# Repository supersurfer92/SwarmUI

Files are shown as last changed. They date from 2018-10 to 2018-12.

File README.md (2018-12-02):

# BadukBot: Swarming robots to play the game Go/Baduk

Based on Zooids: Building Blocks for Swarm User Interfaces

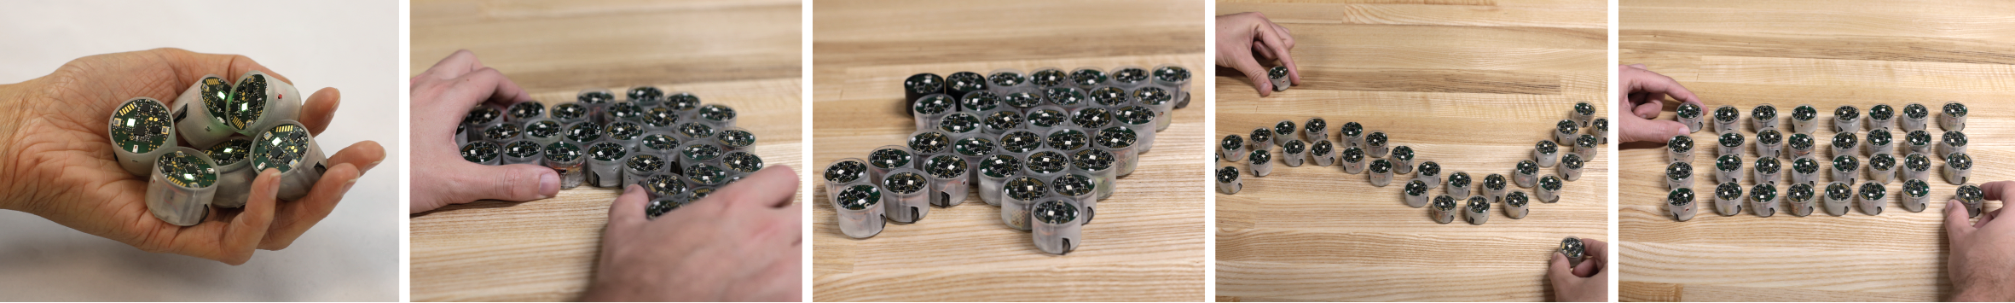
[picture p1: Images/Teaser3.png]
Teaser

Zooids, an open-source open-hardware platform for developing tabletop swarm interfaces, consist of a collection of custom-designed wheeled micro robots (each 2.6 cm in diameter), a radio base-station, a highspeed DLP structured light projector for optical tracking, and a software framework for application development and control.

Initial sketch of the redesigned Zooid, the BadukBot:
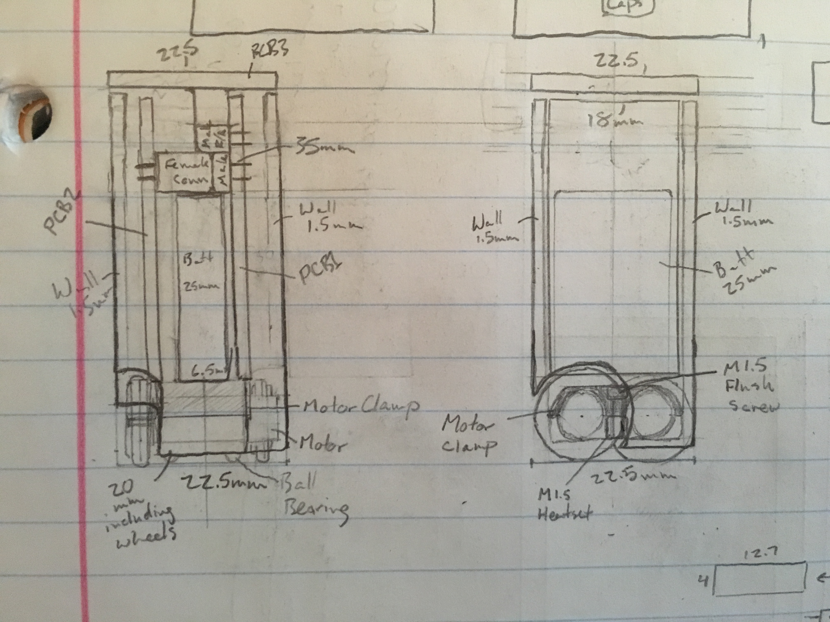
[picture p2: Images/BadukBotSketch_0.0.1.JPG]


Revision 3 of the new pcb:
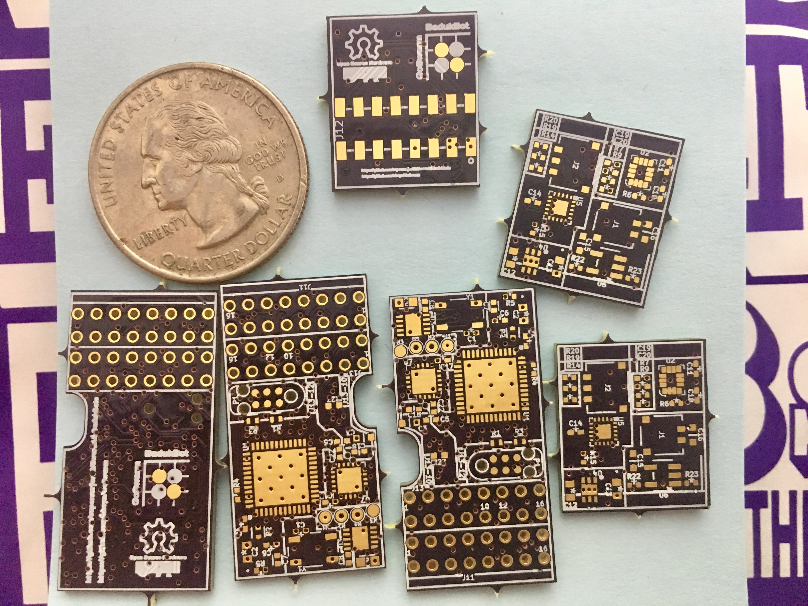
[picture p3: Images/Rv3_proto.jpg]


Original board:

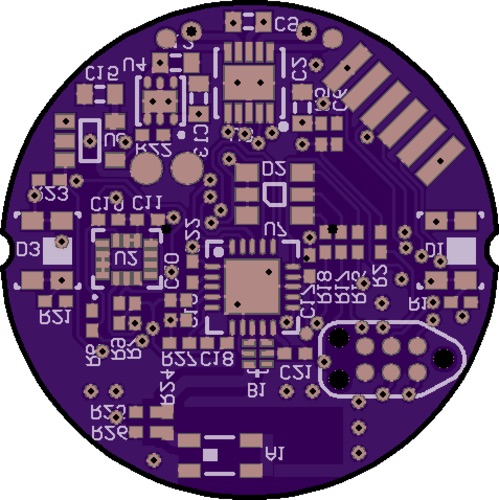
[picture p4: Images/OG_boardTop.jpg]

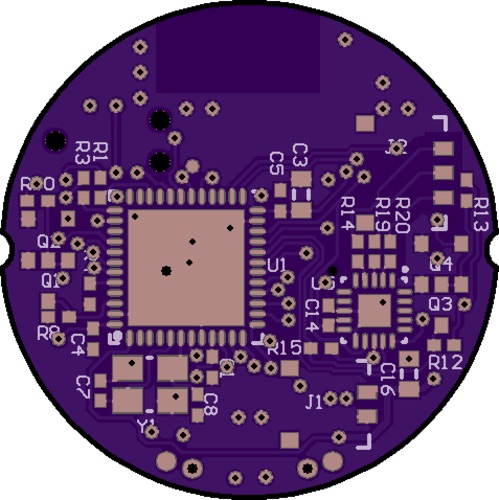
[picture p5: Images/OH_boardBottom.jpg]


BadukBot is based on Zooid software and hardware modified to play the game Go/Baduk/Weiqi. https://en.wikipedia.org/wiki/Go_(game)

Zooids in action: https://www.youtube.com/watch?time_continue=125&v=ZVdAfDMP3m0

IMAGE ALT TEXT (http://www.youtube.com/watch?v=ZVdAfDMP3m0 "Zooids: Building Blocks for Swarm User Interfaces")

## Hardware
<p align="center">
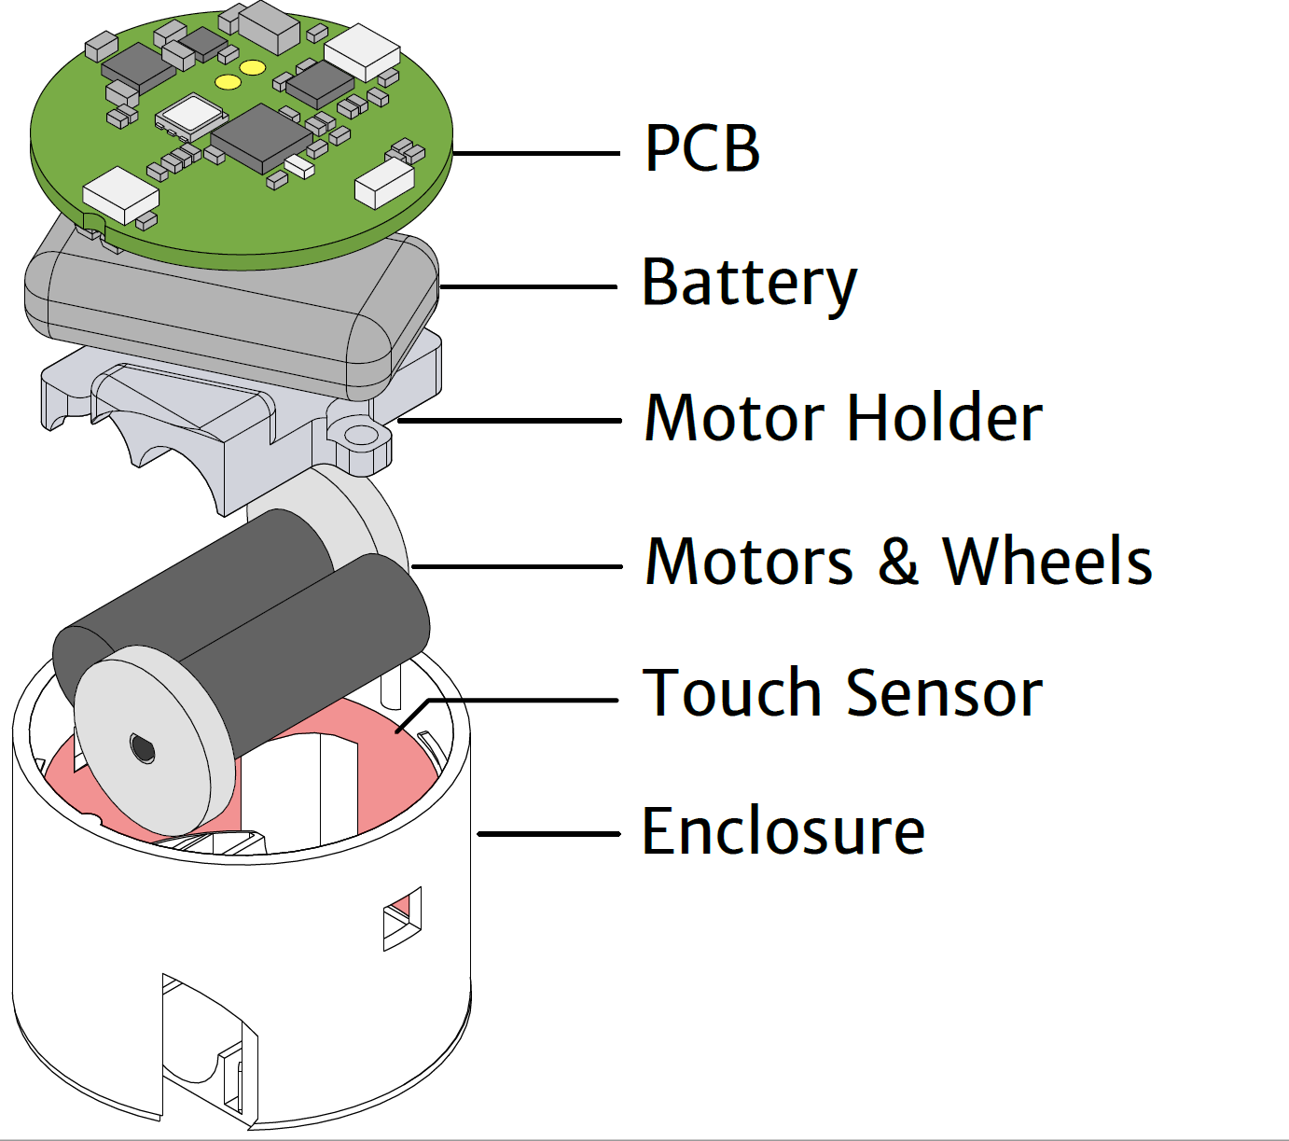
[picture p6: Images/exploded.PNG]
exploded

</p>

The original Zooids are small custom-made robots as shown above; their dimensions are 26 mm in diameter, 21 mm in height
and they weight about 12 g. Each robot is powered by a 100 mAh LiPo battery and uses motor driven wheels. They contain a flexible elctrode for capacitive touch sensing. It communicates with the main computer through a NRF24L01+ chip on a separate receiver. Currently the limit for bots per receiver is 10. More can be added at a cost to performance/communication speed.

BadukBots are 22.5 mm in diameter and ~50 mm in height. Each bot is powered by a 200 mAh lipo battery with motor driven wheels.

The original Zooid files have been converted from Altium schematics to KiCAD from scratch based on the original Zooid schematic pdf (original files break when converted.) The new PCBs and schematics are located in the BadukBot directory. The Proto...BOM consolidates the components for bots, Receivers, chargers, and tools required into one sheet. The new BOM is mostly the same with changes to include prices, links, and modifications to quantities to make 81 (for a 9x9 board) and 361 (for a 19x19 board) bots in the Master BOM spreadsheet.

The PCB is designed using KiCAD and FreeRouting. The 3D files are created in MODO. The BadukBot breaks the design into 3 single boards that encase the battery to both make it possible to reflow at home and reduce the foot print to 22.5 mm from the Zooid's 26 mm (go stones are 22.5 mm and allow for a full 19x19 board to fit in the projection area.) Dimensions for bots and the playspace are based on https://senseis.xmp.net/?EquipmentDimensions and will be scaled if needed accordingly.

We may try other DLP Lightcrafter EVMs to reduce cost ($140 vs $1400.)

### Tracking
The system uses a projector-based tracking system for robot position tracking as shown below. Using a high frame rate (3000Hz) projector (DLP LightCrafter Evaluation Module) from Texas Instruments Inc., a sequence of gray-coded patterns are projected onto a flat surface. Then, the photodiodes on the robot independently decodes into a location within the projected area. 
The instruction for setting up this projector-based tracking system is included in the repository. 
There are other DLPLCEVM projectors available at lower resolutions and refresh rates ranging from $140 to $1600.

The play area will be mapped to make a main play area, a go bowl area and a capture pieces area

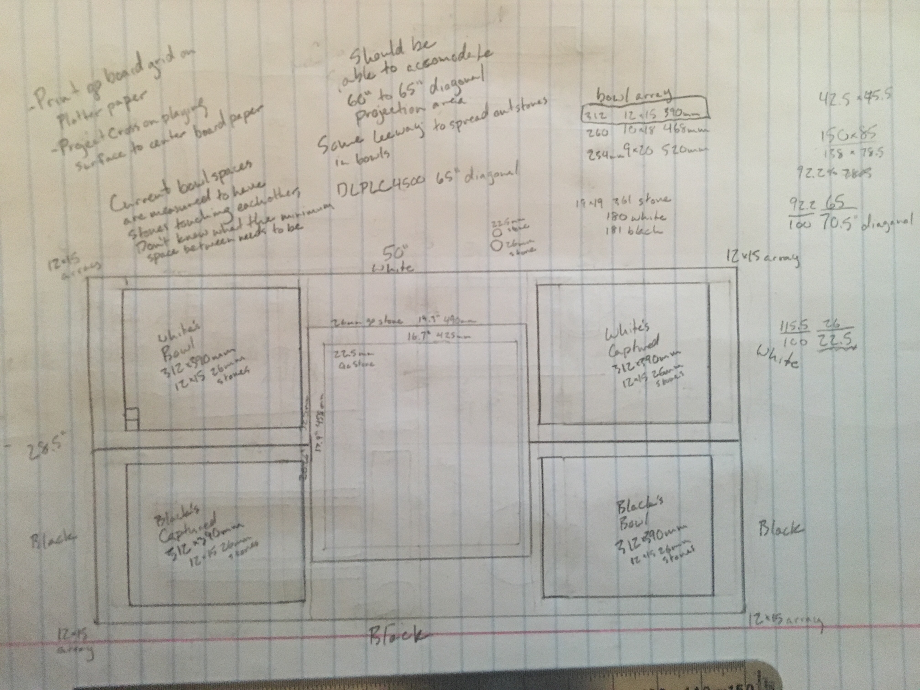
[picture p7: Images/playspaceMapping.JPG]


## Software
<p align="center">
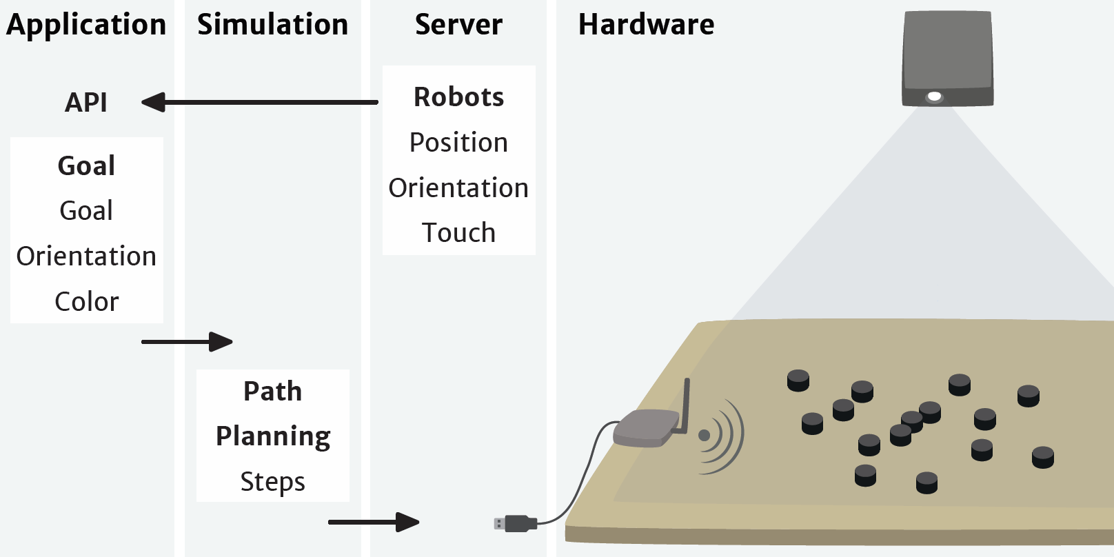
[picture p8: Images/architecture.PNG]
architecture

</p>

The communication structure consists of four main layers from highest to lowest level: Application, Simulation, Server, and Hardware. 

At the application level, the desired positions of the robots are computed. These desired positions are transmitted to
the simulation layer through a network socket. The application programmer can choose between two control strategies:
Proportional-Integral-Derivative (PID) position control or Hybrid Reciprocal Velocity Obstacles (HRVO) combined
with PID (these options are explained in the next paragraphs). Based on the chosen control strategy, the simulation layer
computes the goal positions of the robots, either final positions for PID or intermediate points for HRVO, and sends them to
the server. Finally, the server layer dispatches commands to the individual zooids, while at the same time monitoring their status and position.

Each robot independently controls its motion through a PID controller based on the state machine shown below. Given a final goal, the robot initially turns itself in the right direction and, once aligned, accelerates to its user-defined preferred speed. When it reaches the speed, it maintains it with a PID control on the orientation to ensure its direction towards the final goal. When a new incremental goal is given, it will still move at same speed but the PID control on orientation will direct the robot towards the new intermediate goal. When the robot arrives within 5 cm of the final goal, it slows down to its minimum velocity and once within 1 cm of the final goal, it stops and orients itself as commanded by the application programmer. To enable smooth transitions between the incremental goal positions, robots are given their next position at 60 Hz.

The modified software for playing Go using SwarmUI (GoSwarm) can be found at https://github.com/nheyn/GoSwarm and https://github.com/nheyn/react-swarm-ui and modified firmware will be maintained in this repo.

Goals include:

-defined areas for the bots including game play area on a grid

-automatically arranging bots to a Go bowl area

-automatically moving captured stones/bots to a defined captured bowl area

-queueing bots for the next turn

-game play rules like passing/resigning

-automatic scoring (and the ability to adjust captured areas)

-the ability to show which player is the winner (2 bots emerge from the winners go bowl, 1 from the loser after both sides pass or one resigns)

Resources and goals for features can be found at https://github.com/supersurfer92/SwarmUI-BadukBots/blob/master/Software/Go%20Features%2C%20Programming%20Gits%2C%20and%20theory.txt

GoSwarm has rewritten the ZooidManager program from C++ to Java and is currently developing swarming functions

IMAGE ALT TEXT (https://youtu.be/S-AZOblyv-w "GoSwarm BadukBot playing behavior test")

<p align="center">
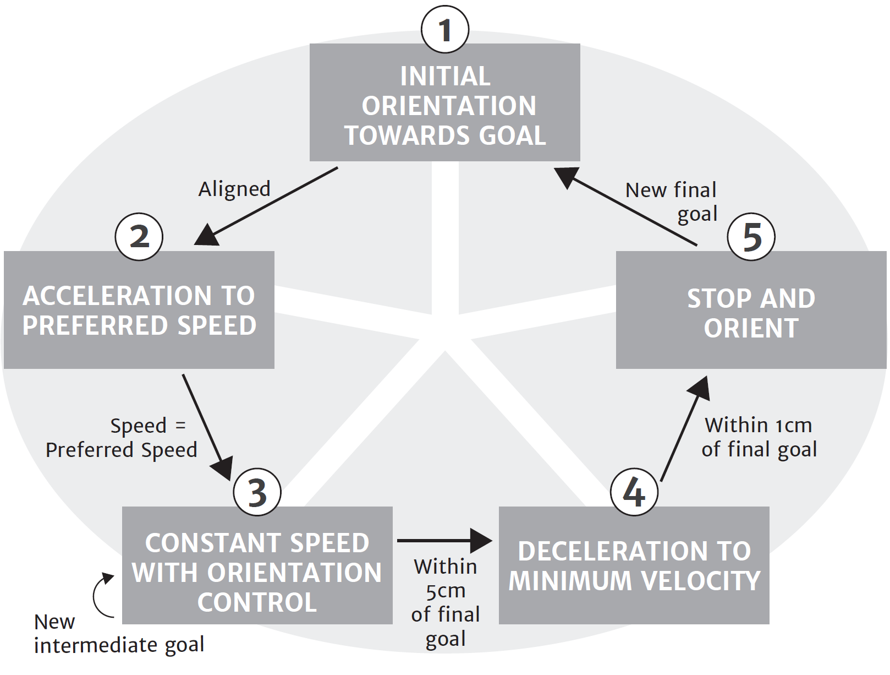
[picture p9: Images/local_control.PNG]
control

</p>

## Acknowledgments 

BadukBot and GoSwarm/react-SwarmUI is a hobby project created by Caleb Cover and Nick Heyn based on SwarmUI.

The original SwarmUI project (https://github.com/ShapeLab/SwarmUI) is a joint work between the Shape Lab at Stanford University (USA) and the Aviz team at Inria (France). It was partially funded by the Région Ile de France, DIM ISC-PIF. We would also like to thank Alexa Siu, Shenli Yuan, Ernesto Ramirez and Pham Minh Hieu for investing so much time and efforts in making this work possible. 

The original licenses are retained where applicable and the licenses used for new hardware developed will use a license that follows the Open Source Hardware Association definition of Open Source Hardware (https://www.oshwa.org/definition/.)

<p align="center">
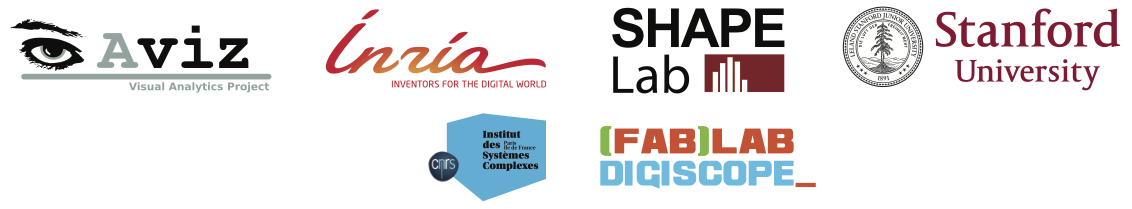
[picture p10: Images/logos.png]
logos

</p>

<br />This work is licensed under a <a rel="license" href="http://creativecommons.org/licenses/by-sa/4.0/">Creative Commons Attribution-ShareAlike 4.0 International License</a>.

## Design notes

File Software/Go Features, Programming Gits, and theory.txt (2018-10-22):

Swarm Function ideas:

-Have swarm automatically move captured stones to captured area/”bowl” and then self rearrange
-Automatically organize swarm into “go bowl” area (probably should use 2 receivers, one for black and one for white and assign unique Ids like 1b, 2b, 1w, 2w, etc)
-Have “go bowl” swarm automatically pop one out for next move after playing current move/during other player's turn
-Go bowl and captured areas each need to have space for 41 to 181 bots on each players side (something like 4x5 array and 13x14, can change ratios to make everything fit in projected space)
-Automatically score game(can manually move pieces to make adjustments/score corrections), winner has two bots move from go bowl and loser has 1 move out
-Pass function (put the bot that popped out back into the go bowl)
-Resign function (take two bots out of resignee's captured bots bowl)

Go programming resources

List of resources on Github
https://github.com/waltheri/go-libraries

Optical position recognition for go
https://github.com/tomasmcz/imago

Neural network for playing go (1 player vs Com)
https://github.com/jmoudrik/deep-go-wrap
https://chrisc36.github.io/deep-go/
https://github.com/joway/DeepNeuralNetworkGo 
(and a computer to go with it, can be built for less than listed in article)
https://www.oreilly.com/learning/build-a-super-fast-deep-learning-machine-for-under-1000

PvP in C++
https://github.com/velvokay/BadukGen

Top level/general Go functions
https://www.britgo.org/gopcres/program

Skinny prototype idea:
-create new pcb on based on original schematics (go from horizontal planar circle to verticle square profile that matches the battery.)
-use micro quadcopter 110mAh battery (10% higher capacity, long and skinny that can be mounted vertically to reduce footprint)
-Skrink BadukBot's enclosure to match as close as possible to actual "official" go stone size (current foot print is 26mm, "official" stone diameter 22.5 mm)
-Make PCB single sided so a cheap reflow setup like this can be used https://hackaday.com/2017/07/13/a-bright-idea-for-reflow-soldering/
(less than $30/lamp using Harbor Freight halogen lamps that should be able to reflow 4-6 boards each[orders of magnitude better than 1 board at a time using hot air soldering for each side; can etch a couple boards using Arapahoe Library's Makerspace for free to make the reflow; they have a 3D printer, laser cutter, cnc, and basic small electronics tools)
*can do something a bit larger in scale with: https://hackaday.com/2012/03/08/toaster-oven-reflow-soldering-roundup/*
-Can use smaller motors like https://www.alibaba.com/product-detail/Coreless-Ultra-small-planetary-reduction-6mm_60804644083.html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 to reduce footprint by 2-4mm if firmware can be modified from 25:1 @ 1200 rpm to 136:1 @ 250 rpm. Can do 700:1 @ 45rpm to reduce by 4-6 mm but probably too slow (close to a regular 19x19 size play space though.) 
-Change touch sensor so it has same surface area as Zooid, but change it from a ring to a helical coil around proto bat/board
-Would need to go from current charging board to the smaller profile/need to go from lasercut acrylic to 3D printed frame to hold upside down bots to charge.

**EXCELLENT RESOURCES FOR START TO FINISH SMALL TO MEDIUM RUN ELECTRONIC MANUFACTURING**
-Testing/Programming/Firmware flashing: https://hackaday.com/2016/08/24/tools-of-the-trade-test-and-programming/
-Through hole soldering: https://hackaday.com/2016/07/22/tools-of-the-trade-through-hole-assembly/
-Inspection: https://hackaday.com/2016/06/29/tools-of-the-trade-inspection/
-Reflow: https://hackaday.com/2016/06/02/tools-of-the-trade-reflow/
-Component Placing: https://hackaday.com/2016/05/10/tools-of-the-trade-component-placing/
-Solder paste dispensing: https://hackaday.com/2016/03/10/tools-of-the-trade-solder-paste-dispensing/
-Multiboard stencils: https://hackaday.com/2018/07/07/multi-board-solder-stencils-explained/

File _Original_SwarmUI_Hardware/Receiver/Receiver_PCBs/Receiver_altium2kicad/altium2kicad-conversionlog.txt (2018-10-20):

Archive:  db/5164.zip
  inflating: db/5164/ZooidReceiverPCB.PcbDoc  
  inflating: db/5164/._ZooidReceiverPCB.PcbDoc  
  inflating: db/5164/ZRMicrocontroller.SchDoc  
  inflating: db/5164/._ZRMicrocontroller.SchDoc  
  inflating: db/5164/ZRPeripherals.SchDoc  
  inflating: db/5164/._ZRPeripherals.SchDoc  
  inflating: db/5164/ZRRadio.SchDoc  
  inflating: db/5164/._ZRRadio.SchDoc  
Loading ZRMicrocontroller.SchDoc

Loading ZRPeripherals.SchDoc

Loading ZRRadio.SchDoc

Loading ZooidReceiverPCB.PcbDoc

Done.
Handling ZooidReceiverPCB-PcbDoc/Root Entry/FileHeader.dat
Handling ZRMicrocontroller-SchDoc/Root Entry/FileHeader.dat
Handling ZRPeripherals-SchDoc/Root Entry/FileHeader.dat
Handling ZRRadio-SchDoc/Root Entry/FileHeader.dat
WARNING: Elliptical arcs are not supported in KiCad - creating circular arc using average radius instead
Handling ZRMicrocontroller.SchDoc
Handling ZRPeripherals.SchDoc
Handling ZRRadio.SchDoc
Handling ZooidReceiverPCB-PcbDoc/Root Entry/Board6/Data.dat
ASCII-ZooidReceiverPCB-PcbDoc.PcbDoc exists?
Writing to ZooidReceiverPCB-PcbDoc/Root Entry/Board6/Data.dat.txt
Writing to ZooidReceiverPCB-PcbDoc/Root Entry/Models/Data.dat.txt
Writing to ZooidReceiverPCB-PcbDoc/Root Entry/UniqueIDPrimitiveInformation/Data.dat.txt
Writing to ZooidReceiverPCB-PcbDoc/Root Entry/Rules6/Data.dat.txt
Writing to ZooidReceiverPCB-PcbDoc/Root Entry/Classes6/Data.dat.txt
Writing PCB to ZooidReceiverPCB-PcbDoc.kicad_pcb
Writing to ZooidReceiverPCB-PcbDoc/Root Entry/Nets6/Data.dat.txt
Writing to ZooidReceiverPCB-PcbDoc/Root Entry/Components6/Data.dat.txt
Pads6...
Writing to ZooidReceiverPCB-PcbDoc/Root Entry/ComponentBodies6/Data.dat.txt
NOT FOUND: User Library-Johnson Components SMA - 50 Ohm Connectors 142-0701-801.wrl
NOT FOUND: 27979.wrl
NOT FOUND: 480372200.wrl
Writing to ZooidReceiverPCB-PcbDoc/Root Entry/ShapeBasedComponentBodies6/Data.dat.txt
Writing to ZooidReceiverPCB-PcbDoc/Root Entry/Components6/Data.dat.txt
Where did the model come from? componentid: 0
Where did the model come from? componentid: 1
Where did the model come from? componentid: 2
Where did the model come from? componentid: 3
Where did the model come from? componentid: 4
Where did the model come from? componentid: 5
Where did the model come from? componentid: 6
Where did the model come from? componentid: 7
Where did the model come from? componentid: 8
Where did the model come from? componentid: 9
Where did the model come from? componentid: 10
Where did the model come from? componentid: 11
Where did the model come from? componentid: 12
Where did the model come from? componentid: 13
Where did the model come from? componentid: 14
Where did the model come from? componentid: 15
Where did the model come from? componentid: 16
Where did the model come from? componentid: 17
Where did the model come from? componentid: 18
Where did the model come from? componentid: 19
Where did the model come from? componentid: 20
Where did the model come from? componentid: 21
Where did the model come from? componentid: 22
Where did the model come from? componentid: 23
Where did the model come from? componentid: 24
Where did the model come from? componentid: 25
Where did the model come from? componentid: 26
Where did the model come from? componentid: 27
Where did the model come from? componentid: 28
Where did the model come from? componentid: 29
Where did the model come from? componentid: 30
Where did the model come from? componentid: 31
Where did the model come from? componentid: 32
Where did the model come from? componentid: 33
Where did the model come from? componentid: 34
Where did the model come from? componentid: 35
Where did the model come from? componentid: 36
Where did the model come from? componentid: 37
Where did the model come from? componentid: 38
Where did the model come from? componentid: 39
Where did the model come from? componentid: 40
Where did the model come from? componentid: 41
Where did the model come from? componentid: 42
Where did the model come from? componentid: 43
Where did the model come from? componentid: 44
Writing to ZooidReceiverPCB-PcbDoc/Root Entry/Arcs6/Data.dat.txt
Writing to ZooidReceiverPCB-PcbDoc/Root Entry/Vias6/Data.dat.txt
Writing to ZooidReceiverPCB-PcbDoc/Root Entry/Polygons6/Data.dat.txt
Writing to ZooidReceiverPCB-PcbDoc/Root Entry/Tracks6/Data.dat.txt
Writing to ZooidReceiverPCB-PcbDoc/Root Entry/FileVersionInfo/Data.dat.txt
Writing to ZooidReceiverPCB-PcbDoc/Root Entry/Fills6/Data.dat.txt
Writing to ZooidReceiverPCB-PcbDoc/Root Entry/Regions6/Data.dat.txt
Texts6...

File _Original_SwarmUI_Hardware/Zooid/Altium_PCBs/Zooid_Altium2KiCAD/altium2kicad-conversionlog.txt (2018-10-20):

Archive:  db/5162.zip
  inflating: db/5162/ZooidMicrocontroller.SchDoc  
  inflating: db/5162/._ZooidMicrocontroller.SchDoc  
  inflating: db/5162/ZooidPCB.PcbDoc  
  inflating: db/5162/._ZooidPCB.PcbDoc  
  inflating: db/5162/ZooidPeripherals.SchDoc  
  inflating: db/5162/._ZooidPeripherals.SchDoc  
  inflating: db/5162/ZooidRadio.SchDoc  
  inflating: db/5162/._ZooidRadio.SchDoc  
Loading ZooidMicrocontroller.SchDoc

Loading ZooidPeripherals.SchDoc

Loading ZooidRadio.SchDoc

Loading ZooidPCB.PcbDoc

Done.
Handling ZooidMicrocontroller-SchDoc/Root Entry/FileHeader.dat
Handling ZooidPCB-PcbDoc/Root Entry/FileHeader.dat
Handling ZooidPeripherals-SchDoc/Root Entry/FileHeader.dat
Handling ZooidRadio-SchDoc/Root Entry/FileHeader.dat
Handling ZooidMicrocontroller.SchDoc
Handling ZooidPeripherals.SchDoc
Handling ZooidRadio.SchDoc
Handling ZooidPCB-PcbDoc/Root Entry/Board6/Data.dat
ASCII-ZooidPCB-PcbDoc.PcbDoc exists?
Writing to ZooidPCB-PcbDoc/Root Entry/Board6/Data.dat.txt
Writing to ZooidPCB-PcbDoc/Root Entry/Models/Data.dat.txt
Writing to ZooidPCB-PcbDoc/Root Entry/UniqueIDPrimitiveInformation/Data.dat.txt
Writing to ZooidPCB-PcbDoc/Root Entry/Rules6/Data.dat.txt
Writing to ZooidPCB-PcbDoc/Root Entry/Classes6/Data.dat.txt
Writing PCB to ZooidPCB-PcbDoc.kicad_pcb
Writing to ZooidPCB-PcbDoc/Root Entry/Nets6/Data.dat.txt
Writing to ZooidPCB-PcbDoc/Root Entry/Components6/Data.dat.txt
Pads6...
Writing to ZooidPCB-PcbDoc/Root Entry/ComponentBodies6/Data.dat.txt
NOT FOUND: 781710002.wrl
NOT FOUND: SOT23.wrl
NOT FOUND: 27979.wrl
NOT FOUND: 781710003.wrl
Writing to ZooidPCB-PcbDoc/Root Entry/ShapeBasedComponentBodies6/Data.dat.txt
Writing to ZooidPCB-PcbDoc/Root Entry/Components6/Data.dat.txt
Where did the model come from? componentid: 0
Where did the model come from? componentid: 1
Where did the model come from? componentid: 2
Where did the model come from? componentid: 3
Where did the model come from? componentid: 4
Where did the model come from? componentid: 5
Where did the model come from? componentid: 6
Where did the model come from? componentid: 7
Where did the model come from? componentid: 8
Where did the model come from? componentid: 9
Where did the model come from? componentid: 10
Where did the model come from? componentid: 11
Where did the model come from? componentid: 12
Where did the model come from? componentid: 13
Where did the model come from? componentid: 14
Where did the model come from? componentid: 15
Where did the model come from? componentid: 16
Where did the model come from? componentid: 17
Where did the model come from? componentid: 18
Where did the model come from? componentid: 19
Where did the model come from? componentid: 20
Where did the model come from? componentid: 21
Where did the model come from? componentid: 22
Where did the model come from? componentid: 23
Where did the model come from? componentid: 24
Where did the model come from? componentid: 25
Where did the model come from? componentid: 26
Where did the model come from? componentid: 27
Where did the model come from? componentid: 28
Where did the model come from? componentid: 29
Where did the model come from? componentid: 30
Where did the model come from? componentid: 31
Where did the model come from? componentid: 32
Where did the model come from? componentid: 33
Where did the model come from? componentid: 34
Where did the model come from? componentid: 35
Where did the model come from? componentid: 36
Where did the model come from? componentid: 37
Where did the model come from? componentid: 38
Where did the model come from? componentid: 39
Where did the model come from? componentid: 40
Where did the model come from? componentid: 41
Where did the model come from? componentid: 42
Where did the model come from? componentid: 43
Where did the model come from? componentid: 44
Where did the model come from? componentid: 45
Where did the model come from? componentid: 46
Where did the model come from? componentid: 47
Where did the model come from? componentid: 48
Where did the model come from? componentid: 49
Where did the model come from? componentid: 50
Where did the model come from? componentid: 51
Where did the model come from? componentid: 52
Where did the model come from? componentid: 53
Where did the model come from? componentid: 54
Where did the model come from? componentid: 55
Where did the model come from? componentid: 56
Where did the model come from? componentid: 57
Where did the model come from? componentid: 58
Where did the model come from? componentid: 59
Where did the model come from? componentid: 60
Where did the model come from? componentid: 61
Where did the model come from? componentid: 62
Where did the model come from? componentid: 63
Where did the model come from? componentid: 64
Where did the model come from? componentid: 65
Where did the model come from? componentid: 66
Where did the model come from? componentid: 67
Where did the model come from? componentid: 68
Where did the model come from? componentid: 69
Where did the model come from? componentid: 70
Where did the model come from? componentid: 71
Where did the model come from? componentid: 72
Writing to ZooidPCB-PcbDoc/Root Entry/Arcs6/Data.dat.txt
Writing to ZooidPCB-PcbDoc/Root Entry/Vias6/Data.dat.txt
Writing to ZooidPCB-PcbDoc/Root Entry/Polygons6/Data.dat.txt
Writing to ZooidPCB-PcbDoc/Root Entry/Tracks6/Data.dat.txt
Writing to ZooidPCB-PcbDoc/Root Entry/FileVersionInfo/Data.dat.txt
Writing to ZooidPCB-PcbDoc/Root Entry/Fills6/Data.dat.txt
Writing to ZooidPCB-PcbDoc/Root Entry/Regions6/Data.dat.txt
Texts6...
Unmapped Layers:
"KEEPOUT"=>"Eco1.User"

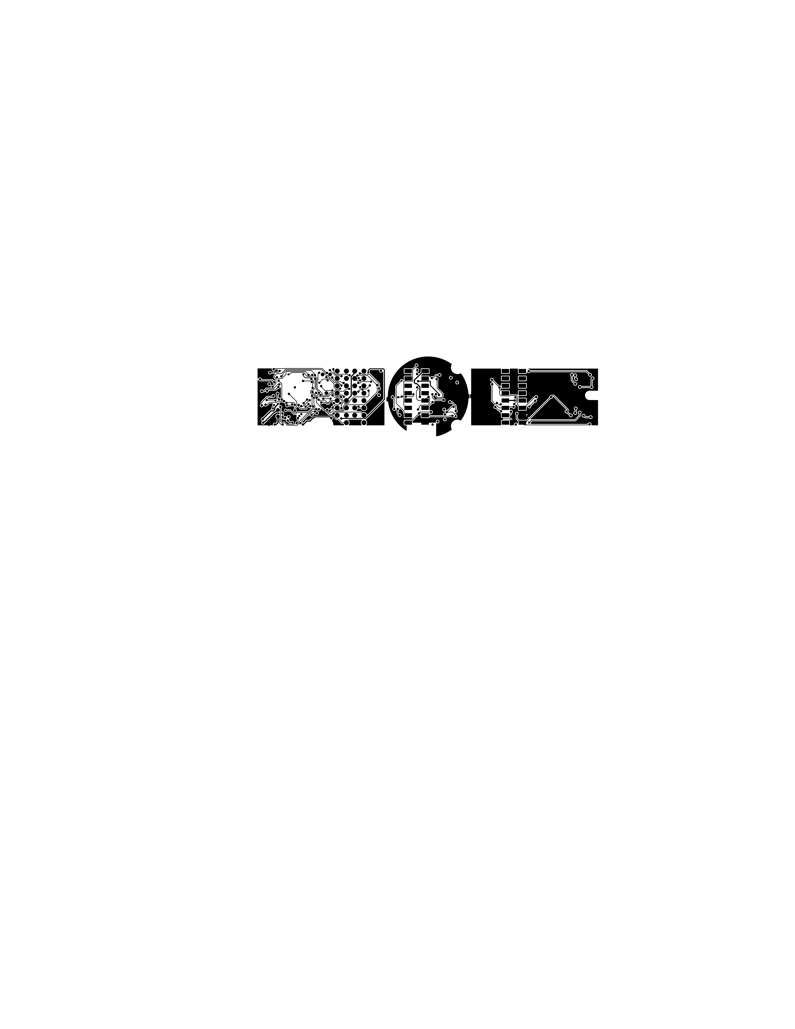
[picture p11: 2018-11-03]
Images/Kicad_board_drawings/BotSchematicRouted_v02-B.Cu.jpg

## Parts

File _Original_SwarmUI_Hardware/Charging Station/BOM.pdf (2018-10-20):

Designator | Quantity | Reference | Description | Supplier URL
*1 thru *50 | 50 0907-9-15-20-75-14-11-0 SMD spring loaded pins | https://www.digikey.com/products/en?keywords=0907-9-15-20-75-14-11-0
J1 | | 1 PJ-002AH-SMT-TR | Power Jack 2.1mm connector | https://www.digikey.com/product-detail/en/cui-inc/PJ-002AH-SMT-TR/CP-002AHPJCT-ND/669692
S1 | | 1 100SP1T1B4M2QE | Toggle Switch | https://www.digikey.com/products/en?keywords=100SP1T1B4M2QE
1 SMI18-5-V-P5R | 5V 15W AC/DC External Wall Mount Adapter https://www.digikey.com/product-detail/en/cui-inc/SMI18-5-V-P5R/102-3677-ND/5417768

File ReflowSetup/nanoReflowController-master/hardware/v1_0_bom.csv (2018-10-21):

Reference | Quantity | Value | Footprint
ARDUINO_NANO1 | 1 | arduino_nano_header | arduino_nano_header
BZ1 | 1 | Buzzer | Buzzer_12x9.5RM7.6
C1 | 1 | 10n 1000v | C_Disc_D4.3mm_W1.9mm_P5.00mm
C2 | 1 | 100n | C_1206_HandSoldering
D1 | 1 | 1N4007 | (for the fan interface, not yet used)D_A-405_P5.08mm_Vertical_AnodeUp
F1 | 1 | Fuse | Fuseholder5x20_horiz_open_inline_Type-I
J1 | 1 | AC IN 220v | TerminalBlock_Pheonix_MKDS1.5-2pol
J10 | 1 | CONN_01X17 | Pin_Header_Straight_1x17_Pitch2.54mm
J2 | 1 | HEATER | TerminalBlock_Pheonix_MKDS1.5-2pol
J3 | 1 | DC IN 12V | TerminalBlock_Pheonix_MKDS1.5-2pol
J4 | 1 | 12v FAN | Pin_Header_Straight_2x01_Pitch2.54mm
J11 J5 J6 J7 J8 | 5 | CONN_01X03 | Pin_Header_Straight_1x03_Pitch2.54mm
J9 | 1 | CONN_01X05 | Pin_Header_Straight_1x05_Pitch2.54mm
JP1 | 1 | VIN enabler | Pin_Header_Straight_1x02_Pitch2.54mm
KK1 | 1 | TRIAC HEATSINK | (optional) SK_09_20_SA_TO_220
OK1 | 1 | H11AA1 | DIP-6_W7.62mm_LongPads
Q1 | 1 | IRF540N | (for the fan interface, not yet used) TO-220_Vertical
R1 R2 | 2 | 47k 0.6w | R_Axial_DIN0207_L6.3mm_D2.5mm_P7.62mm_Horizontal
R3 | 1 | 2.4k | R_Axial_DIN0207_L6.3mm_D2.5mm_P7.62mm_Horizontal
R4 | 1 | 180R | R_Axial_DIN0207_L6.3mm_D2.5mm_P7.62mm_Horizontal
R5 | 1 | 1k | R_Axial_DIN0207_L6.3mm_D2.5mm_P7.62mm_Horizontal
R6 | 1 | 4K7 | (for the fan interface, not yet used) R_Axial_DIN0309_L9.0mm_D3.2mm_P12.70mm_Horizontal
R7 | 1 | 100K | (for the fan interface, not yet used) R_1206_HandSoldering
TRIAC1 | 1 | BT137 | TO-220_Vertical_BT137
U1 | 1 | MOC3020M | DIP-6_W7.62mm_LongPads

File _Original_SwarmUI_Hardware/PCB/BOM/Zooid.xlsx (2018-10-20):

Designator | Quantity | Description | Supplier 1 | Supplier Part Number 1 | Supplier 2 | Supplier Part Number 2
A1 | 1 | JOHANSON TECHNOLOGY 2450AT18D0100 ANTENNA, CERAMIC, 2.45GHZ | Mouser | 609-2450AT18D0100E | Digi-Key | 712-1573-1-ND
B1 | 1 | Johanson Technology Impedance Matched Balun Filter Integrated Passive for nRF24L01 | Farnell | 2148533 | Digi-Key | 712-1574-1-ND
C1, C19 | 2 | 10nF 0402 X7R 25V ±5% | Farnell | 1692285 | Digi-Key | 399-1279-1-ND
C2, C12, C13 | 3 | 1uF 0603 X5R 10V ±10% | Farnell | 1759399 | Digi-Key | 478-1251-1-ND
C3, C15, C16 | 3 | 4.7uF 0603 X5R 10V ±10% | Farnell | 2362098 | Digi-Key | 445-5170-1-ND
C4, C5, C6, C10, C11, C14, C17, C18 | 8 | 100nF 0402 X7R 16V ±10% | Farnell | 1288252 | Digi-Key | 399-3521-1-ND
C7, C8 | 2 | 22pF 0402 NP0/CG0 50V ±5% | Farnell | 1414580 | Digi-Key | 490-5868-1-ND
C9 | 1 | 10uF 0603 X5R 6.3V ±20% | Farnell | 2456110 | Digi-Key | 490-10475-1-ND
C20 | 1 | 1nF 0402 X7R 50V ±10% | Farnell | 1414573 | Digi-Key | 399-1032-1-ND
C21 | 1 | 2.2nF 0402 X7R 50V ±10% | Farnell | 1414582 | Digi-Key | 399-3068-1-ND
C22 | 1 | 33nF 0402 X7R 50V ±10% | Farnell | 2210826 | Digi-Key | 445-7334-1-ND
D1, D3 | 2 | Everlight PD15-22C/TR8 Silicon PIN Photodiode |  |  | Digi-Key | 1080-1367-1-ND
D2 | 1 | ROHM SMLVN6RGB1W1 LED Tri-Color Blue/Green/Red Chip LED 6-Pin 1411 T/RLED Tri-Color Blue/Green/Red Chip LED 6-Pin 1411 | Mouser | 755-SMLVN6RGB1W1 | Digi-Key | 846-1187-1-ND
J1 | 1 | Molex Pico-EZmateô Wire-to-Board Header, 2 contacts | Farnell | 2313710 | Digi-Key | WM4459CT-ND
J2 | 1 | Molex Pico-EZmateô Wire-to-Board Header, 3 contacts | Farnell | 2313562 | Digi-Key | WM5409CT-ND
Q1, Q2, Q3, Q4 | 4 | On Semiconductor MMBT3904L General Purpose Transistor NPN Silicon | Farnell | 1459100 | Digi-Key | MMBT3904LT1GOSCT-ND
R1, R2, R3 | 3 | 22R 0402 1/16W ±1% | Farnell | 2072797 | Digi-Key | 541-22.0LCT-ND
R4, R5, R6, R8, R12, R15, R23 | 7 | 100K 0402 1/16W ±1% | Farnell | 2072519 | Digi-Key | 541-100KLCT-ND
R7, R9, R14, R19, R20, R22 | 6 | 10K 0402 1/16W ±1% | Farnell | 2072517 | Digi-Key | 541-10.0KLCT-ND
R10, R13 | 2 | 560K 0402 1/16W ±1% | Farnell | 2074116 | Digi-Key | 311-560KLRCT-ND
R11, R21 | 2 | 1.5M 0402 1/16W ±1% | Farnell | 2141473 | Digi-Key | 541-1.50MLCT-ND
R16 | 1 | 22.6R 0402 1/16W ±0.05R | Farnell | 2302454 | Digi-Key | P22.6LCT-ND
R17 | 1 | 130R 0402 1/16W ±0.05R | Farnell | 2059115 | Digi-Key | P130LCT-ND
R18 | 1 | 24.9R 0402 1/16W ±0.05R | Farnell | 2059102 | Digi-Key | P24.9LCT-ND
R24 | 1 | 0R 0402 1/16W ±0.05R | Farnell | 2072513 | Digi-Key | P0.0JCT-ND
R27 | 1 | 22K 0402 1/16W ±1% | Farnell | 2072781 | Digi-Key | 541-22.0KLCT-ND
U1 | 1 | STMICROELECTRONICS STM32F051C8U6 MCU 32BIT CORTEX-M0 48MHZ UFQFPN-48 | Farnell | 2393638 | Digi-Key | STM32F051C8U6-ND
U2 | 1 | STMicroelectronics iNEMO inertial module: 3D accelerometer and 3D gyroscope | Farnell | 2474253 | Digi-Key | 497-15383-1-ND
U3 | 1 | ALLEGRO MICROSYSTEMS - A3901SEJTR-T - IC, MOTOR DRIVER | Farnell | 1651947 | Digi-Key | 620-1159-1-ND
U4 | 1 | Analog Devices ADP122ACPZ-3.3-R7 - 5.5 V Input, 300 mA, Low Quiescent Current, CMOS Linear Regulator | Farnell | 2457164 | Digi-Key | ADP122ACPZ-3.3-R7CT-ND
U5 | 1 | Atmel Seven-channel QTouchÆ Touch Sensor IC |  |  | Digi-Key | AT42QT1070-MMHCT-ND
U6 | 1 | Miniature Single-Cell, Fully Integrated Li-Ion, Li-Polymer Charge Management Controller, 4.2V, 5-Pin SOT-23, Industrial Temperature, Tape and Reel | Farnell | 1332158
U7 | 1 | Nordic Semi Ultra low power 2.4GHz RF Transceiver IC |  |  | Digi-Key | 1490-1033-1-ND
Y1 | 1 | TXC - 7V-16.000MAAE-T, 16MHZ, 30PPM, 12PF - CRYSTAL | Farnell | 1892172 | Digi-Key | 887-1462-1-ND

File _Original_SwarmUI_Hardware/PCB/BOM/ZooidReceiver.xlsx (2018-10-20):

Designator | Quantity | Description | Supplier 1 | Supplier Part Number 1 | Supplier 2 | Supplier Part Number 2
A1 | 1 | JOHNSON 142-4701-801 SMA FEMELLE REVERSE POLARITY TERMINAISON | Farnell | 2340523 | Digi-Key | J917-ND
B1 | 1 | Johanson Technology Impedance Matched Balun Filter Integrated Passive for nRF24L01 | Farnell | 2148533 | Digi-Key | 712-1574-1-ND
C1, C14 | 2 | 10nF 0402 X7R 25V ±5% | Farnell | 1692285 | Digi-Key | 399-1279-1-ND
C2, C10, C11 | 3 | 1uF 0603 X5R 10V ±10% | Farnell | 1759399 | Digi-Key | 478-1251-1-ND
C3 | 1 | 4.7uF 0603 X5R 10V ±10% | Farnell | 2362098 | Digi-Key | 445-5170-1-ND
C4, C5, C6, C7, C12, C13 | 6 | 100nF 0402 X7R 16V ±10% | Farnell | 1288252 | Digi-Key | 399-3521-1-ND
C8, C9, C18, C19 | 4 | 22pF 0402 NP0/CG0 50V ±5% | Farnell | 1414580 | Digi-Key | 490-5868-1-ND
C15 | 1 | 1nF 0402 X7R 50V ±10% | Farnell | 1414573 | Digi-Key | 399-1032-1-ND
C16 | 1 | 2.2nF 0402 X7R 50V ±10% | Farnell | 1414582 | Digi-Key | 399-3068-1-ND
C17 | 1 | 33nF 0402 X7R 50V ±10% | Farnell | 2210826 | Digi-Key | 445-7334-1-ND
D1 | 1 | ROHM SMLVN6RGB1W1 LED Tri-Color Blue/Green/Red Chip LED 6-Pin 1411 T/RLED Tri-Color Blue/Green/Red Chip LED 6-Pin 1411 | Mouser | 755-SMLVN6RGB1W1 | Digi-Key | 846-1187-1-ND
D2 | 1 | BRIGHT BLUE LED 20mA | Farnell | 1716770 | Digi-Key | 160-1646-1-ND
J1 | 1 | Molex USB 2.0 Connector Plug USB Type A | Farnell | 2313729 | Digi-Key | WM3983CT-ND
R1, R2, R3, R9 | 4 | 22R 0402 1/16W ±1% | Farnell | 2072797 | Digi-Key | 541-22.0LCT-ND
R4, R5 | 2 | 100K 0402 1/16W ±1% | Farnell | 2072519 | Digi-Key | 541-100KLCT-ND
R6 | 1 | 22.6R 0402 1/16W ±0.05R | Farnell | 2302454 | Digi-Key | P22.6LCT-ND
R7 | 1 | 130R 0402 1/16W ±0.05R | Farnell | 2059115 | Digi-Key | P130LCT-ND
R8 | 1 | 24.9R 0402 1/16W ±0.05R | Farnell | 2059102 | Digi-Key | P24.9LCT-ND
R10 | 1 | 0R 0402 1/16W ±0.05R | Farnell | 2072513 | Digi-Key | P0.0JCT-ND
R13 | 1 | 22K 0402 1/16W ±1% | Farnell | 2072781 | Digi-Key | 541-22.0KLCT-ND
R14 | 1 | 1M 0402 1/16W ±1% | Farnell | 2072521 | Digi-Key | P1.00MLCT-ND
R15 | 1 | 1.5K 0402 1/16W ±1% | Farnell | 1653201 | Digi-Key | 541-1.50KLCT-ND
U1 | 1 | STMICROELECTRONICS STM32F103CBU6 ARM Cortex-M3, 72 MHz, 128 KB, 20 KB, 48, VFQFPN | Farnell | 2060891 | Mouser | 511-STM32F103CBU6
U2 | 1 | Analog Devices ADP122ACPZ-3.3-R7 - 5.5 V Input, 300 mA, Low Quiescent Current, CMOS Linear Regulator | Farnell | 2457164 | Digi-Key | ADP122ACPZ-3.3-R7CT-ND
U3 | 1 | Nordic Semi Ultra low power 2.4GHz RF Transceiver IC |  |  | Digi-Key | 1490-1033-1-ND
Y1, Y2 | 2 | TXC - 7V-16.000MAAE-T, 16MHZ, 30PPM, 12PF - CRYSTAL | Farnell | 1892172 | Digi-Key | 887-1462-1-ND
 | 1 | Antenna 2.4GHZ | Mouser | 888-A24-HASM-450 | Digi-Key | A24-HASM-450-ND

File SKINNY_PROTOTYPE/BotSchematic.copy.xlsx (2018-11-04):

Prj: | BadukBot_Schematic |  |  |  |  |  | Board Qty: | 100
Co.: | Converted to KiCAD by Caleb Cover |  |  |  |  |  | Unit Cost: | $0.00
Prj date: | Thursday, November 01, 2018 at 11:16:31 PM |  |  |  |  |  | Total Cost: | $0.00
$ date: | 2018-11-02 16:40:18
Global Part Info
Refs | Value | Desc | Footprint | Manf | Manf# | Qty | Unit$ | Ext$
A1 | 2450AT18D0100E |  | 2450AT18D0100E:DFN320X160X120-4RN |  | 2450AT18D0100E (https://www.mouser.com/datasheet/2/611/2450AT18D0100-1130385.pdf) | 0 |  | $0.00
B1 | nrf24l01 |  |  |  | 2450BM14A0002T | 0 |  | $0.00
C1,C19 | 10nF |  | 10nF:C0402C103J3RACTU |  | C0402C103J3RACTU | 0 |  | $0.00
C11 | 100nF |  |  |  | LMK107BJ475KA-T | 0 |  | $0.00
C12,C13 | 1uF |  |  |  | 0603ZD105KAT2A | 0 |  | $0.00
C16 | Taiyo |  | TAIYO_YUDEN_LMK107BJ475KA-T_0 |  | CL10A475KP8NNNC | 0 |  | $0.00
C2 | 1uF |  | 1uF:0603ZD105KAT2A |  | 0603ZD105KAT2A | 0 |  | $0.00
C20 | 1nF |  | 100nf:C0402C104K4RACTU |  | C0402C102K5RACTU | 0 |  | $0.00
C21 | 22nF |  |  |  | C0402C222K5RACTU | 0 |  | $0.00
C22 | 33nF |  | 33nF:CAPC1005X55N |  | CGA2B3X7R1H333K050BB | 0 |  | $0.00
C3,C15 | TAIYO_YUDEN_LMK107BJ475KA-T |  | TAIYO_YUDEN_LMK107BJ475KA-T:TAIYO_YUDEN_LMK107BJ475KA-T_0 |  | CL10A475KP8NNNC | 0 |  | $0.00
C7,C8 | 22pF |  | 22pf_GRM1555C1H220JA01D:CAPC1005X55N |  | GRM1555C1H220JA01D | 0 |  | $0.00
C9 | 10uF |  | 10uF:CAPC1608X9N |  | GRM188R61A106ME9D | 0 |  | $0.00
C4-C6,C10,C14,C17,C18 | 100nF |  | 100nf:C0402C104K4RACTU |  | LMK107BJ475KAT | 0 |  | $0.00
D1,D3 | PD15-22C_TR8 | PHOTODIODE PIN IR CLEAR FLAT SMD | digikey-footprints:SMD-4_3.3x2.8_PD15-22C_TR8 | Everlight Electronics Co Ltd | PD1522CTR8 (https://media.digikey.com/pdf/Data%20Sheets/Everlight%20PDFs/PD15-22C_TR8.pdf) | 0 |  | $0.00
D2 | SMLVN6RGB1W1 |  | SMLVN6RGB1W1:LED310X280X60-6N |  | SMLVN6RGB1W1 | 0 |  | $0.00
J1 | MOLEX781710002 |  | MOLEX_78171-0002:MOLEX_78171-0002_0 |  | 781710002 | 0 |  | $0.00
J10 | A316DA2SV71 |  | A13:A13 |  | A316DA2SV71 (https://www.digikey.com/product-detail/en/hirose-electric-co-ltd/A3-16DA-2SV-71/H10966-ND/1033093) | 0 |  | $0.00
J11 | 62401621722 |  | 16pos_2mm_RA:0877601616 |  | 0877601616 (https://www.digikey.com/product-detail/en/molex-llc/0877601616/WM18618-ND/662457) | 0 |  | $0.00
J12 | A316DA2SV71 |  | A13:A13_1 |  | A316DA2SV71 | 0 |  | $0.00
J13 | 0877601616 |  | 16pos2mmRA:62401621722 |  | 0877581616 | 0 |  | $0.00
J2 | MOLEX781710003 |  | MOLEX_78171-0003:MOLEX_78171-0003_0 |  | 781710003 | 0 |  | $0.00
Q1-Q4 | MMBT3904LT1G | TRANS NPN 40V 0.2A SOT23 | digikey-footprints:SOT-23-3 | ON Semiconductor | MMBT3904LT1G (http://www.onsemi.com/pub/Collateral/MMBT3904LT1-D.PDF) | 0 |  | $0.00
R10,R13 | 560K |  | 560K:RC0402FR-07560KL |  | RC0402FR-07560KL | 0 |  | $0.00
R11,R21 | 1.5M |  | 1.5M:CRCW04021M50FKED |  | CRCW04021M50FKED | 0 |  | $0.00
R14,R19,R20 | 10K |  | 10K0402:CRCW040210K0FKED |  | CRCW040210K0FKED | 0 |  | $0.00
R16 | 22.6R |  | 22_6R:ERJ-2RKF22R6X |  | ERJ2RKF22R6X | 0 |  | $0.00
R17 | 130R |  | 130R:ERJ-2RKF1300X |  | RVC0402FT130K | 0 |  | $0.00
R18 | 24.9R |  | 24.9R:ERJ-2RKF24R9X |  | ERJ2RKF24R9X | 0 |  | $0.00
R24 |  |  |  |  | RC0402JR-070RL | 0 |  | $0.00
R27 | 22K |  | 22K:RESC1005X40N |  | CRCW040222K0FKED | 0 |  | $0.00
R4,R5,R8,R12,R15 | 100K |  | 100K:CRCW0402100KFKED |  | CRCW0402100KFKED | 0 |  | $0.00
R6,R23 | 100K |  |  |  | CRCW0402100KFKED | 0 |  | $0.00
R7,R9,R22 | 10K |  |  |  | CRCW040210K0FKED | 0 |  | $0.00
R1-R3 | VISHAY_CRCW040222R0FKED |  | 22r:VISHAY_CRCW040222R0FKED_0 |  | MCMR04X22R0FTL | 0 |  | $0.00
U1 | STM32F051C8U6 | STM32F051C8U6 | STM32F051C8U6:QFN50P700X700X65-49N-D |  | STM32F051C8U6 | 0 |  | $0.00
U2 | LSM6DS3 |  |  |  | LSM6DS3TR | 0 |  | $0.00
U3 | A3901SEJTRT |  | A3901SEJTR-T:DFN300X300X75-11N |  | A3901SEJTRT | 0 |  | $0.00
U4 | ADP122ACPZ33R7 | Analog Devices ADP122ACPZ-3.3-R7, LDO Regulator, 300mA, 3.3 V, 1%, 2.3 5.5 Vin 6-Pin, LFCSP UD | ADP122ACPZ-3.3-R7:SON65P200X200X60-7N-D |  | ADP122ACPZ33R7 (http://www.analog.com/media/en/technical-documentation/data-sheets/ADP122_123.pdf) | 0 |  | $0.00
U5 | AT42QT1070MMHCTND |  | vq:VQFN_20PAD |  | AT42QT1070MMHR (http://ww1.microchip.com/downloads/en/DeviceDoc/Atmel-9596-AT42-QTouch-BSW-AT42QT1070_Datasheet.pdf) | 0 |  | $0.00
U6 | MCP73831T2ACIOT |  | MCP:MCP73831T-2ACI&slash_OT |  | MCP73831T2ACIOT (http://ww1.microchip.com/downloads/en/DeviceDoc/20001984g.pdf) | 0 |  | $0.00
U7 | NRF24L01PR7 | IC RF TXRX ISM>1GHZ 20-VFQFN | digikey-footprints:QFN-20-1EP_4x4mm_RevA | Nordic Semiconductor ASA | NRF24L01PR7 (http://www.nordicsemi.com/eng/content/download/2726/34069/file/nRF24L01P_Product_Specification_1_0.pdf) | 0 |  | $0.00
Y1 | 7V16000MAAET |  | TXC-7V-16.000MAAE-T:OSCCC500X320X105N |  | 7V16000MAAET | 0 |  | $0.00
KiCost® v.1.0.4 (Powered by Octopart.com API)

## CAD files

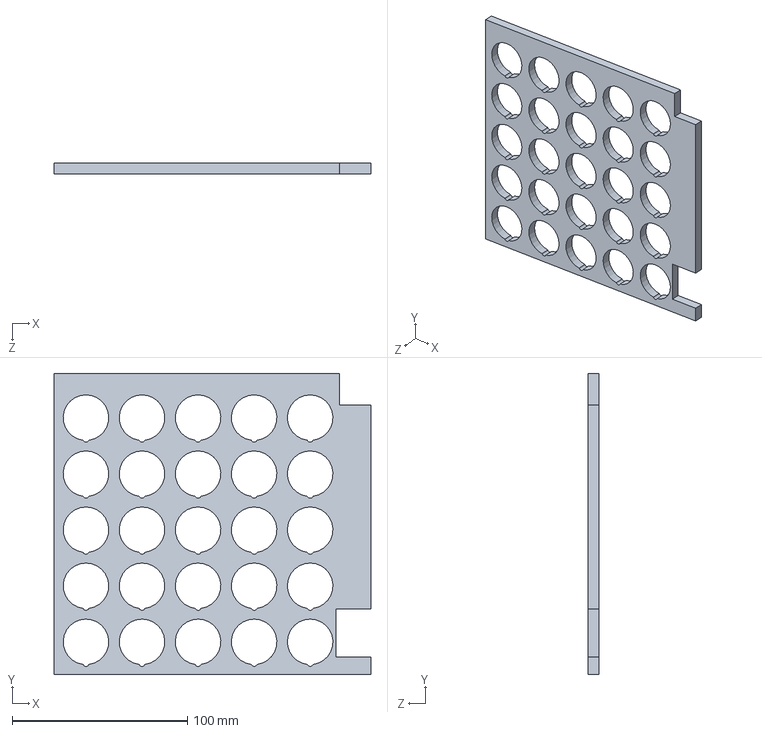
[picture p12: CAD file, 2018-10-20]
_BadukBot/Hardware/3D Model/Charging Station/ChargingStation.SLDPRT
181.0 x 171.9 x 6.35 mm

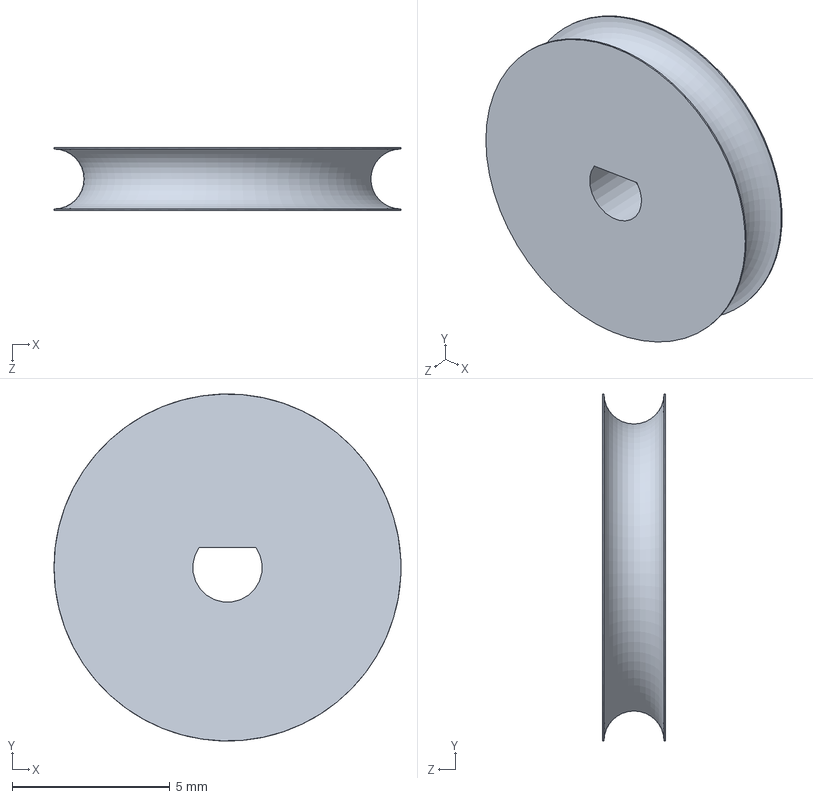
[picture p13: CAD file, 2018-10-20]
_BadukBot/Hardware/3D Model/Robot/WheelWithSlot.SLDPRT
11.0 x 11.0 x 2.00 mm

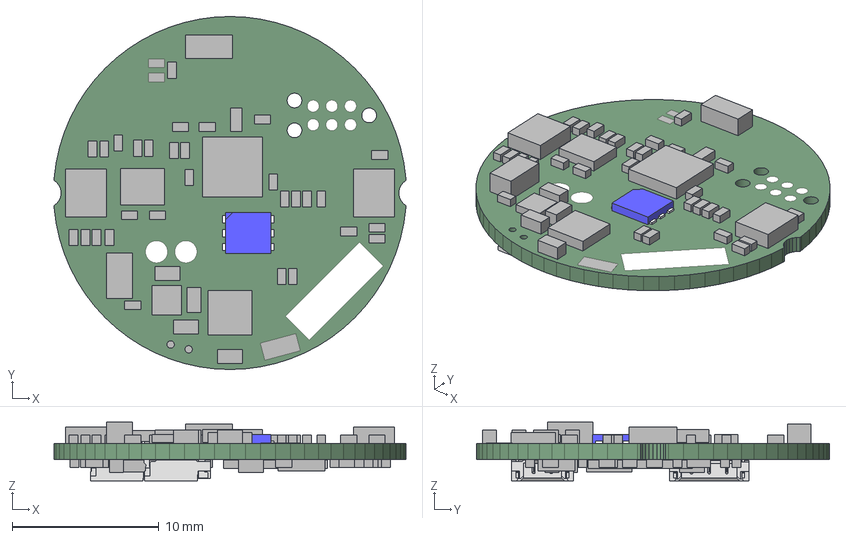
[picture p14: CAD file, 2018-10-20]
_BadukBot/Hardware/3D Model/Zooid_PCB.step
23.9 x 24.0 x 4.01 mm

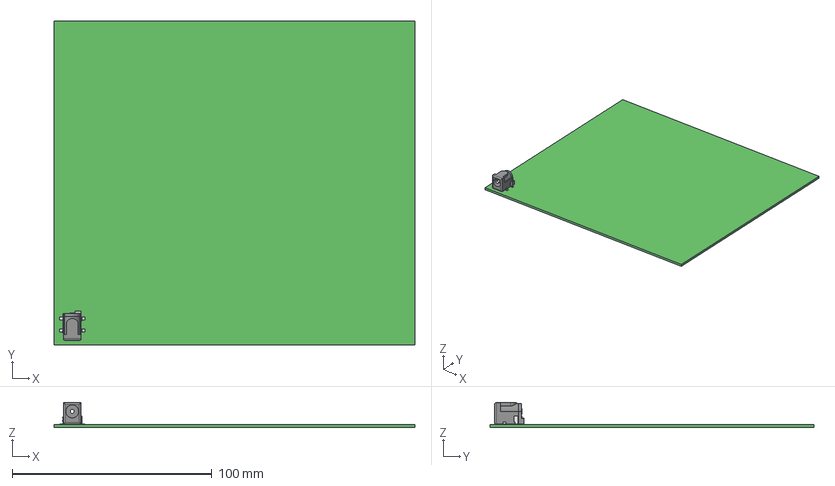
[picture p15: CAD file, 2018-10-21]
_BadukBot/Hardware/Charging Station/Charging.step
180.9 x 162.4 x 12.6 mm
Board
pj-002ah-smt x 7
Extruded

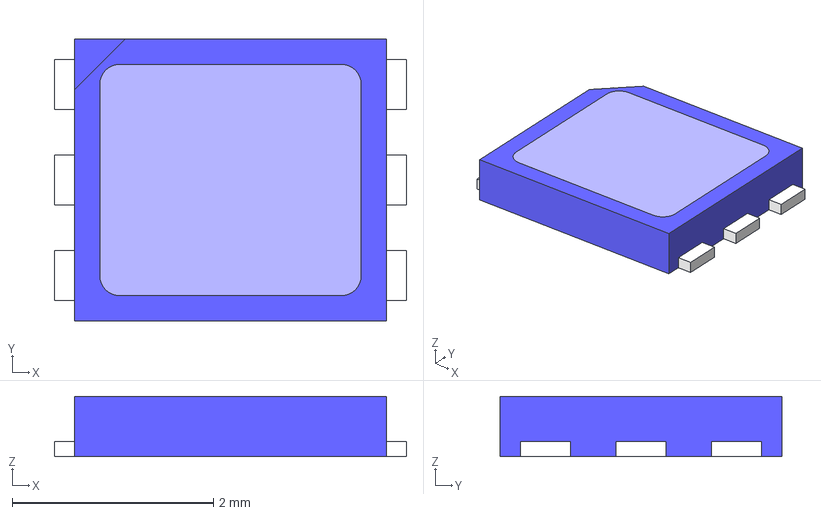
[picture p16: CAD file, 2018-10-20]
_BadukBot/Hardware/Receiver/Receiver_PCBs/Receiver_altium2kicad/ZooidReceiverPCB-PcbDoc/Root Entry/Models/1.dat.step
3.50 x 2.80 x 0.6 mm

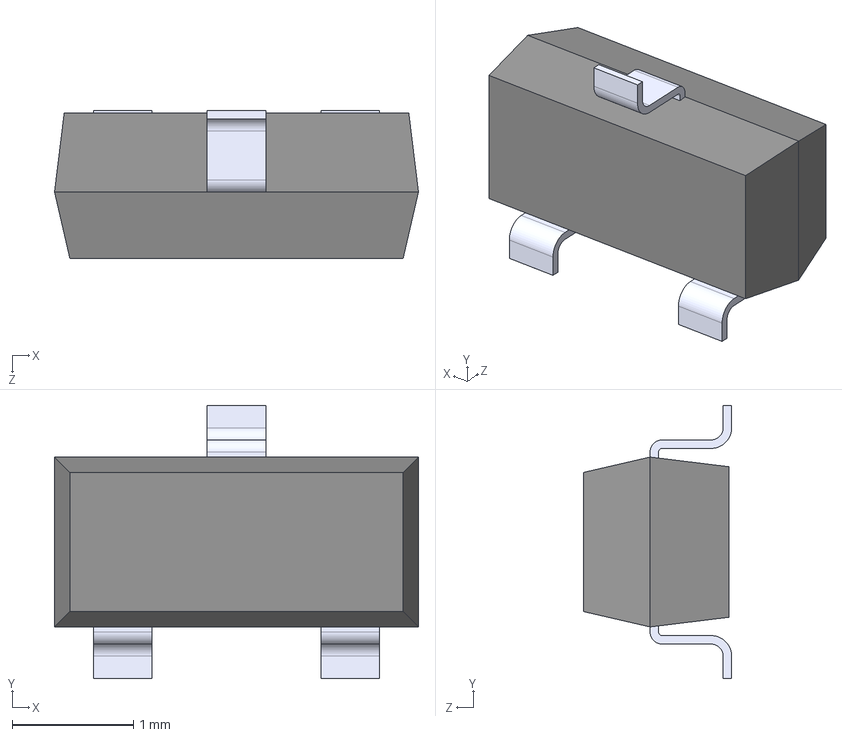
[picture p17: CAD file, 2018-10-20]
_BadukBot/Hardware/Zooid/Altium_PCBs/Zooid_Altium2KiCAD/ZooidPCB-PcbDoc/Root Entry/Models/2.dat.step
3.00 x 2.25 x 1.22 mm

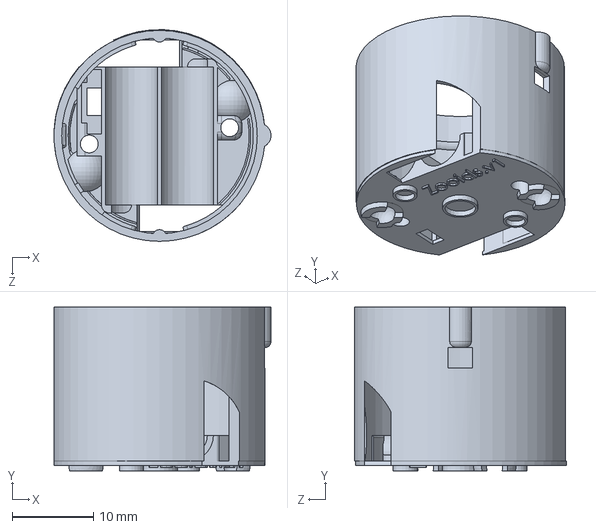
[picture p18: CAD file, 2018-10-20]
SKINNY_PROTOTYPE/Hardware/3D Model/Robot/SmallBase.SLDPRT
26.7 x 20.2 x 26.1 mm

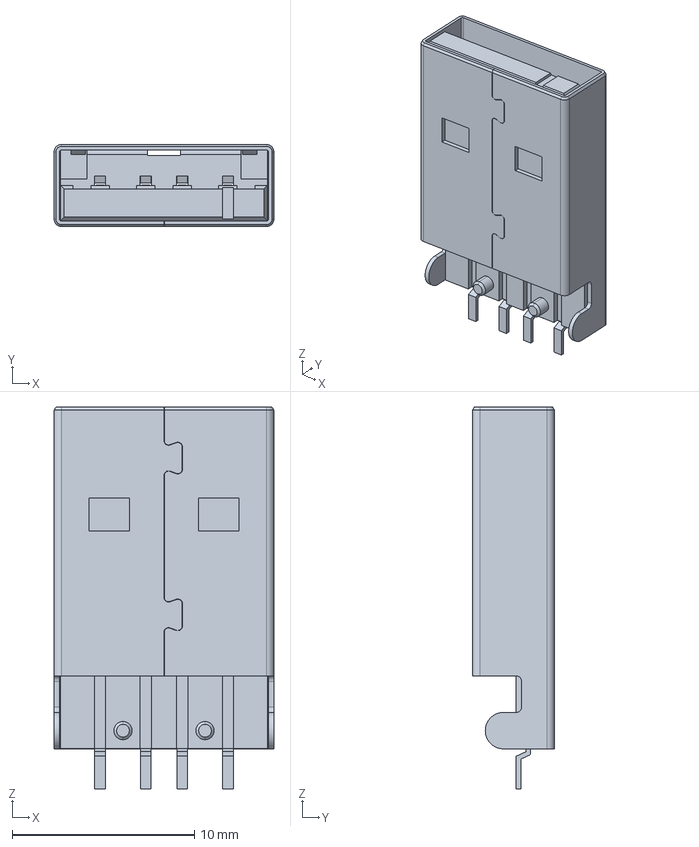
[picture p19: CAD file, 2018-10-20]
SKINNY_PROTOTYPE/Hardware/Receiver/Receiver_PCBs/Receiver_altium2kicad/ZooidReceiverPCB-PcbDoc/Root Entry/Models/2.dat.step
12.1 x 4.50 x 21.0 mm

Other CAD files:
SKINNY_PROTOTYPE/Hardware/3D Model/Charging Station/ChargingStation.DXF
SKINNY_PROTOTYPE/Hardware/3D Model/Robot/SmallBase.STL
SKINNY_PROTOTYPE/Hardware/3D Model/Robot/TopMotor_hole_90mAh.STL
SKINNY_PROTOTYPE/Hardware/3D Model/Robot/TopMotor_hole_90mAh.sldprt
SKINNY_PROTOTYPE/Hardware/3D Model/Robot/WheelWithSlot.STL
SKINNY_PROTOTYPE/Hardware/3D Model/ZooidReceiver_PCB.step
SKINNY_PROTOTYPE/Hardware/Receiver/Receiver_PCBs/Receiver_altium2kicad/ZooidReceiverPCB-PcbDoc/Root Entry/Models/0.dat.step
SKINNY_PROTOTYPE/Hardware/Zooid/Altium_PCBs/Zooid_Altium2KiCAD/ZooidPCB-PcbDoc/Root Entry/Models/1.dat.step
SKINNY_PROTOTYPE/Hardware/Zooid/Altium_PCBs/Zooid_Altium2KiCAD/ZooidPCB-PcbDoc/Root Entry/Models/3.dat.step
_BadukBot/Hardware/3D Model/Charging Station/ChargingStation.DXF
_BadukBot/Hardware/3D Model/Robot/SmallBase.STL
_BadukBot/Hardware/3D Model/Robot/TopMotor_hole_90mAh.STL
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

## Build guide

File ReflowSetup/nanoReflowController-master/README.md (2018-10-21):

Reflow Oven Controller
====================

http://therandomlab.blogspot.com/2017/07/halogen-floodlight-smt-reflow.html

**News**

* Forked from 0xPIT & uploaded the code after a lot of restructuration
* Board design has also changed

**Arduino-based reflow oven controller with:**
* [PID] loop control
* [Wave Packet] control for AC output
* graphic TFT LC-Display, drawing the temperature curves
  * using a 5v compatible 1.8" of 1.44" TFT SPI display with ST7735 controller
* solely controlled using a cheap rotary encoder and its single button
* uses a MAX6675 module as interface to a K type thermocouple
* stores up to 30 temperature profiles in EEPROM
* configurable PID-parameters
* simple, small hardware to drive loads up to 600V and up to 2A without heatsink
* powered throuhg one of three options: 12v RAW pin, 5v pin or 5v USB
* optional 12v fan control (not yet implemented in the code)
* *Please Note*: Requires Arduino IDE 1.5.x or newer

(c) 2017 David Sanz Kirbis
(c) 2014 Karl Pitrich <karl@pitrich.com>
in part based on a project (c) 2013 Ed Simmons <ed@estechnical.co.uk>

## Warning: This project operates with possibly lethal mains voltage. If you are unsure what to do, don't do it and get help from an experienced tinkerer with professional training.

**Minimal build**

BoardPic1 | BoardPic2
------------ | -------------

**Completely populated**

Complete1 | Complete2 | Complete3
------------ | ------------ | -------------

**Enclosed and mounted on halogen floodlight**

(more info: [Halogen Floodlight SMT reflow])

Floodlight
--------------

<!---
**Post action shot**

![CycleWithOverflow] | ![Warning]
------------ | -------------

Introduction
====================

This Reflow Oven Controller relies on an [Arduino Nano] easily obtainable on eb*y for less than $10, plus my custom shield, which is actually more like a motherboard.

As I believe it is not wise to have a mess of wiring and tiny breakout-boards for operating mains powered equipment, I've decided to design custom board with easily obtainable components.

The hardware can be found in the [folder hardware], including the Eagle schematics and PCB layout files. It should fit the freemium version of Eagle. Here are preview images:

![PCB][ImgPCB]
![Schematic][ImgSCH]

The board contains the [Arduino Nano], very simple [Zero crossing] detection circuit, used to align control logic to mains frequency, two [MAX31855] thermocouple-to-digital converters and two [Sharp S202S01] PCB-mount solid state relays, mounted on cheap [Fischer SK409 50,8] heat sinks. The current software uses only one of the thermocouples, so you need to populate one IC only. If you're lucky, you can get free samples of the MAX31855 from Maxim.

The software uses [PID] control of the heater and fan output for improved temperature stability. The heater AC load is controlled using [Wave Packet] control in order to minimize RF interference and load on the relay. For the fan motor, [Phase Fired] control has been implemented.

Please note that all important timings are *based on the mains frequency*, so the circuit will **not work** properly without mains connection.

But for testing, I've added an additional timer to simulate the zero-crossings, in order to run the software without being connected to mains. The software should work in 50 and 60Hz mains, the 60Hz version is not tested, though.

Errata and construction infos
========

Issue | Notes
------------ | -------------

Screenshots and usage information
========

Image | Information
------------ | -------------
![CycleWithOverflow] | *Display after a cylcle has been completed. The blue line is the setpoint, the red line the actual temperature measured by the thermocouple. Note that the graph wraps around automatically. 'Sp' is the current setpoint calculated by the PID loop. In the lower line there are: Current heater and fan outputs, both in percent, and the current temperature rise or drop rate in °C per second. The graph will draw orientation lines every 50°C up to the peak temperature set in the selected profile.*
![MenuDefault] | *The main menu can be navigated by rotating the encoder (sic!). Clicking enters the menu item, or navigates to the submenu. Doubleclick moves up or back or exits the menu item.*
![FanSpeedEdit] | *To edit a setting, click once to enter edit mode (red cursor), then rotate to change the value, click again to save. Doubleclick will exit without saving.*
![MenuEditProfile] | -
![ProfileSettings] | *Typical solder profile settings...*
![ProfileSettingsEdit] | *These parameters can be easily edited using the encoder as described above.*
![MenuLoadProfile] | *Up to 30 Profiles can be loaded and saved. You have to do this manually, so that you can have 'save-as' functionality without overwriting existing profiles.*
![PIDValues] | *Current pid values for my 1300W 20$ toaster oven.*
![PIDValuesEdit] | *Editing is simple, like above. Note that, unlike with the profile settings, the PID values will be automatically stored to EEPROM when you exit the submenu by doubleclicking.*
--->

Obtaining the source code
====================

Get the code using `git`.

	git clone https://github.com/dasaki/nanoReflowController.git

or [download a Snapshot].

I've added some libraries I've used as submodules to the git repositroy, so it is important that, after cloning this repository, you do 

    git submodule update --init

to fetch all involved libraries. (See: [Submodule Cheat Sheet])

Installation
====================

Of course, you need to have the Arduino IDE installed. I've worked with version 1.5.x only and I will not support older versions. Get it from the [Arduino Download] page or upgrade you current Arduino setup.

There as several dependencies you need to install. 

If you are unfamiliar with Arduino Libraries, please read [the library guide].
Basically, each library needs to be liked or copied into your Arduino library folder.

<!---
My code uses [TimerOne] for basic timing, for the 1.8" TFT I've used [Adafruit_ST7735], which requires [Adafruit_GFX]. I **strongly suggest** to use my **modified version** of [Adafruit_ST7735-pit], as it **performs much better**, but requires you to use SPI, which my board does anyway.

For the user interface you require my own [Menu] and [ClickEncoder] libraries, which are included as submodules.

All other libraries need to be downloaded and installed.

After you've installed all libraries, open the Arduino IDE, open the ReflowController.pde sketch (using File->Open).

Select the right hardware from the Tools->Board menu.

Compile the firmware (Sketch->Verify) to test everything is installed correctly. If something's wrong, feel free to post an issue here on github, I will look into it.

Now, choose the correct serial port from Tools->Serial Port and then upload the code.
*Remember* that a standard compile will get stuck at "Calibrating..." without proper mains connection, so that zero crossing interrupts can occur.

I could not fit PID Autotuning into the limited space of the Arduino in addition the normal code. So if you want to try to autotune you PID Loop, install the [PID_AutoTune] Library, `#define PIDTUNE 1` in the .ino file, then recompile and download do the Arduino.

As all timing relies on Zero Crossing detection, you need to `#define FAKE_HW 1` and install [TimerThree] when you want to run without actual hardware *and/or* without mains connection.

Things to note
====================

* The [MAX31855] does not like the thermocouple being grounded; It must be isolated from ground or earth.
* The PID Loop must be tuned individually for each oven. It will *not* work out of the box. 
* [PID Autotune] is not very useful, as it seems to be able to tune only to keep a specific temperature value, which is not what we do in a reflow oven. Also, at least my oven seems to be very non-linear when heating up.
* When rewiring inside your oven, use only wiring that can withstand high temperatures. I use silicone coated lace.
* Do not solder wiring inside you oven, the temperature might desolder you joints. **Crimp everything.**
* Use proper earth ground connection for your ovens chassis.

Ideas and todo
====================
* Optimize code size so that more features can fit
* Clamp values for parameters to reasonalbe ranges
* Add scrollbar (sample implementation in the demo for [Menu]
* Separate PID configuration for each process step
* try to make the display faster, it is very slow
* Named profiles
* Rewrite [Menu] so that is uses callback objects instead of spaghetti-callbacks
--->

Licensing
====================
```
The MIT License (MIT)

Copyright (c) 2017 David Sanz Kirbis
All rights reserved.

Permission is hereby granted, free of charge, to any person obtaining a copy
of this software and associated documentation files (the "Software"), to deal
in the Software without restriction, including without limitation the rights
to use, copy, modify, merge, publish, distribute, sublicense, and/or sell
copies of the Software, and to permit persons to whom the Software is
furnished to do so, subject to the following conditions:

The above copyright notice and this permission notice shall be included in
all copies or substantial portions of the Software.

THE SOFTWARE IS PROVIDED "AS IS", WITHOUT WARRANTY OF ANY KIND, EXPRESS OR
IMPLIED, INCLUDING BUT NOT LIMITED TO THE WARRANTIES OF MERCHANTABILITY,
FITNESS FOR A PARTICULAR PURPOSE AND NONINFRINGEMENT. IN NO EVENT SHALL THE
AUTHORS OR COPYRIGHT HOLDERS BE LIABLE FOR ANY CLAIM, DAMAGES OR OTHER
LIABILITY, WHETHER IN AN ACTION OF CONTRACT, TORT OR OTHERWISE, ARISING FROM,
OUT OF OR IN CONNECTION WITH THE SOFTWARE OR THE USE OR OTHER DEALINGS IN
THE SOFTWARE.
```

[PID Autotune]:https://github.com/br3ttb/Arduino-PID-AutoTune-Library
[Submodule Cheat Sheet]:http://blog.jacius.info/git-submodule-cheat-sheet/
[ESTechnical]:http://www.estechnical.co.uk
[Arduino Download]:http://arduino.cc/en/Main/Software
[folder hardware]:https://github.com/dasaki/nanoReflowController/tree/master/hardware
[download a Snapshot]:https://github.com/dasaki/nanoReflowController/archive/master.zip
[the library guide]:http://arduino.cc/en/Guide/Libraries
[PID]:http://en.wikipedia.org/wiki/PID_controller
[Wave Packet]:http://de.wikipedia.org/wiki/Schwingungspaketsteuerung
[Phase Fired]:http://en.wikipedia.org/wiki/Phase-fired_controllers 
[Adafruit 1.8" TFT]:http://www.adafruit.com/products/358
[MAX31855]:http://www.maximintegrated.com/en/products/analog/sensors-and-sensor-interface/MAX31855.html
[Fischer SK409 50,8]:http://www.pollin.de/shop/dt/NzE5OTY1OTk-
[Sharp S202S01]:http://sharp-world.com/products/device/lineup/data/pdf/datasheet/s102s01_e.pdf
[Zero crossing]:http://en.wikipedia.org/wiki/Zero_crossing
[TimerOne]:http://playground.arduino.cc/Code/Timer1
[TimerThree]:http://playground.arduino.cc/Code/Timer1
[Adafruit_ST7735]:https://github.com/adafruit/Adafruit-ST7735-Library
[Adafruit_GFX]:https://github.com/adafruit/Adafruit-GFX-Library
[Adafruit_ST7735-pit]:https://github.com/0xPIT/Adafruit-ST7735-Library
[Menu]:https://github.com/0xPIT/menu
[ClickEncoder]:https://github.com/0xPIT/encoder
[Arduino Nano]:https://store.arduino.cc/arduino-nano

[CycleWithOverflow]:https://raw.githubusercontent.com/0xPIT/reflowOvenController/master/images/CycleWithOverflow.jpg
[FanSpeedEdit]:https://raw.githubusercontent.com/0xPIT/reflowOvenController/master/images/FanSpeedEdit.jpg
[MenuDefault]:https://raw.githubusercontent.com/0xPIT/reflowOvenController/master/images/Menu.jpg
[MenuLoadProfile]:https://raw.githubusercontent.com/0xPIT/reflowOvenController/master/images/MenuLoadProfile.jpg
[MenuEditProfile]:https://raw.githubusercontent.com/0xPIT/reflowOvenController/master/images/MenuEditProfile.jpg
[PIDValuesEdit]:https://raw.githubusercontent.com/0xPIT/reflowOvenController/master/images/PIDValuesEdit.jpg
[ProfileSettings]:https://raw.githubusercontent.com/0xPIT/reflowOvenController/master/images/ProfileSettings.jpg
[PIDValues]:https://raw.githubusercontent.com/0xPIT/reflowOvenController/master/images/PIDValues.jpg
[ProfileSettingsEdit]:https://raw.githubusercontent.com/0xPIT/reflowOvenController/master/images/ProfileSettingsEdit.jpg

[Warning]:http://www.proshieldsafetysigns.co.uk/signs/59793_signs.jpg
[ImgPCB]:https://raw.githubusercontent.com/0xPIT/reflowOvenController/master/hardware/v0.2.brd.preview.png
[ImgSCH]:https://raw.githubusercontent.com/0xPIT/reflowOvenController/master/hardware/v0.2.sch.preview.png

[ImgMissingTrace]:https://raw.githubusercontent.com/0xPIT/reflowOvenController/master/images/MissingTrace.jpg
[BoardPic1]:https://raw.githubusercontent.com/dasaki/nanoReflowController/master/images/v1_0_Board_picture_top.jpg
[BoardPic2]:https://raw.githubusercontent.com/dasaki/nanoReflowController/master/images/v1_0_Board_picture_bottom.jpg
[Complete1]:https://raw.githubusercontent.com/dasaki/nanoReflowController/master/images/v1_0_Board_3d_01.png
[Complete2]:https://raw.githubusercontent.com/dasaki/nanoReflowController/master/images/v1_0_Board_3d_02.png
[Complete3]:https://raw.githubusercontent.com/dasaki/nanoReflowController/master/images/v1_0_Board_3d_03.png
[Floodlight]:https://raw.githubusercontent.com/dasaki/nanoReflowController/master/images/v1_0_floodlight_reflow.jpg
[Halogen Floodlight SMT reflow]:http://therandomlab.blogspot.com.es/2017/07/halogen-floodlight-smt-reflow.html

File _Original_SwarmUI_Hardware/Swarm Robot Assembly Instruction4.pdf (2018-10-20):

Swarm Robot Assembly Instruction

Components:

1. 3D printed robot base | 2. Motor Holder | 3. 2 M2 x 6 mm Screws (https://www.mcmaster.com/#90116a010/=158pc9a) 4. 2 Metal Balls (https://www.mcmaster.com/#9528k11/=158p8f7)

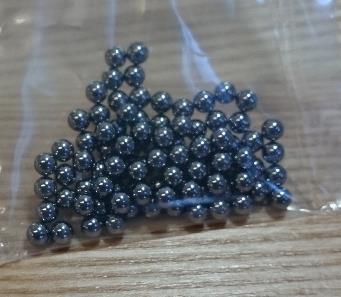
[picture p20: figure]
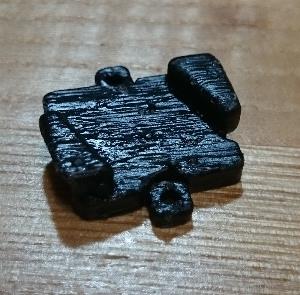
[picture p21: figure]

4. Battery | 5. Switch (http://www.digikey.com/product-detail/en/copal-electronics-inc/CUS-12TB/563-1102-1-ND/1124231) | 6. PCB | 7. 2 Motors (https://www.firgelliauto.com/products/mini-motor-micro-motor)
6.0x12x20mm
100mAh 3.7V (https://bluetaiyang.en.alibaba.com/collection_product/100mah/2.html?isGallery=Y)
(Contact seller for exact model)
8. Wheels (O-ring (https://www.amazon.com/gp/product/B00NJTNT7K/ref=ox_sc_act_title_1?ie=UTF8&psc=1&smid=ATVPDKIKX0DER) + 3D-printed part)

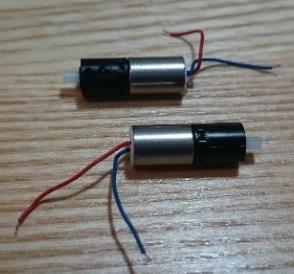
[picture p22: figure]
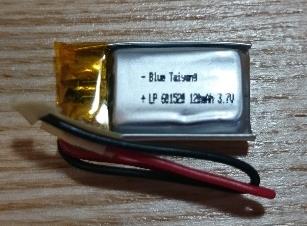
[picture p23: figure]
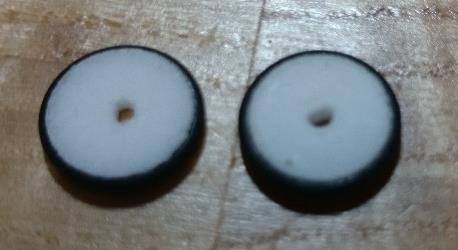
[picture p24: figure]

9. Crimps, (http://www.digikey.com/product-search/en?keywords=WM3992CT-ND) connectors for Power Connector (http://www.digikey.com/product-search/en?keywords=WM4348-ND)/Touch Connector (http://www.digikey.com/product-search/en?keywords=WM3564-ND)

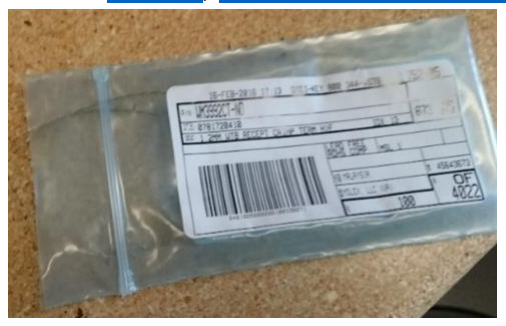
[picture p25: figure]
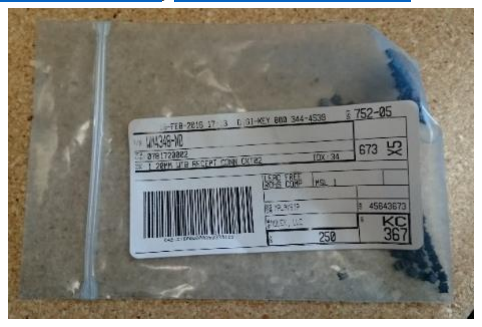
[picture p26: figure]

10. Capacitive touch flexible circuit (https://github.com/ShapeLab/SwarmUI/blob/master/Hardware/3D%20Model/v1/Touch%20Circuit.pdf)

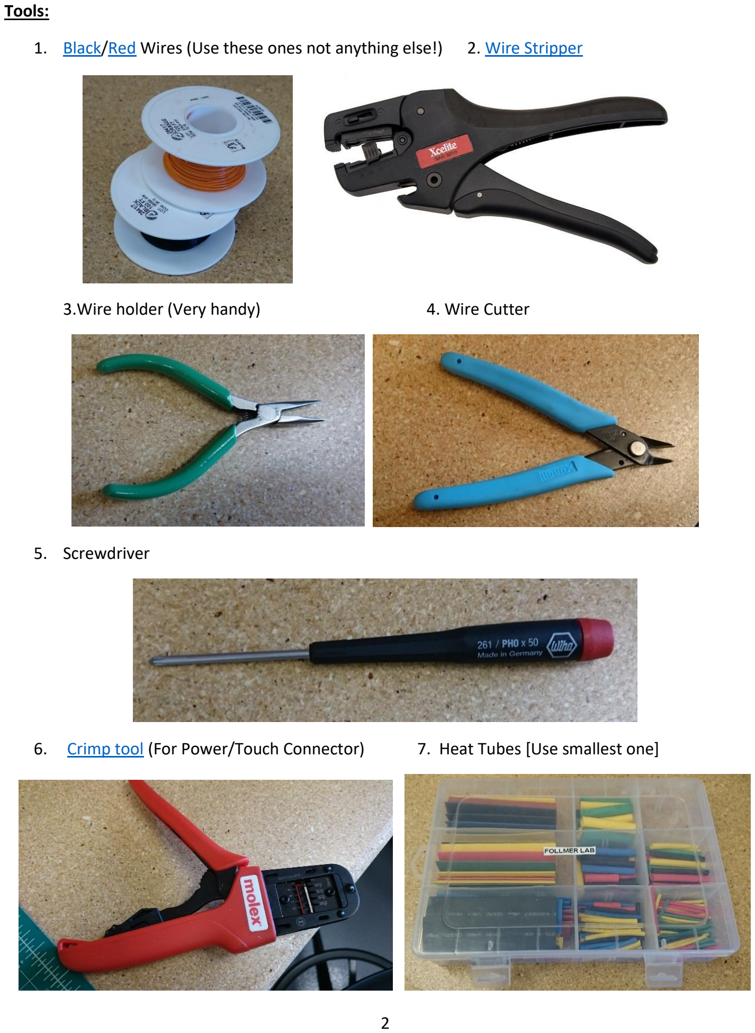
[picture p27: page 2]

Tools:

1. Black/ (http://www.digikey.com/product-search/en?keywords=2842%2F7%20BK005-ND)Red (http://www.digikey.com/product-search/en?keywords=2842%2F7%20RD005-ND) Wires (Use these ones not anything else!) | 2. Wire Stripper (https://www.amazon.com/gp/product/B004UN8ZNM/ref=ox_sc_act_title_1?ie=UTF8&psc=1&smid=ATVPDKIKX0DER)
3.Wire holder (Very handy) | 4. Wire Cutter
5. Screwdriver
6. Crimp tool (http://www.digikey.com/product-search/en?WT.z_cid=sp_900_0310_buynow&keywords=638194300) (For Power/Touch Connector) 7. Heat Tubes [Use smallest one]

Overall Structure:

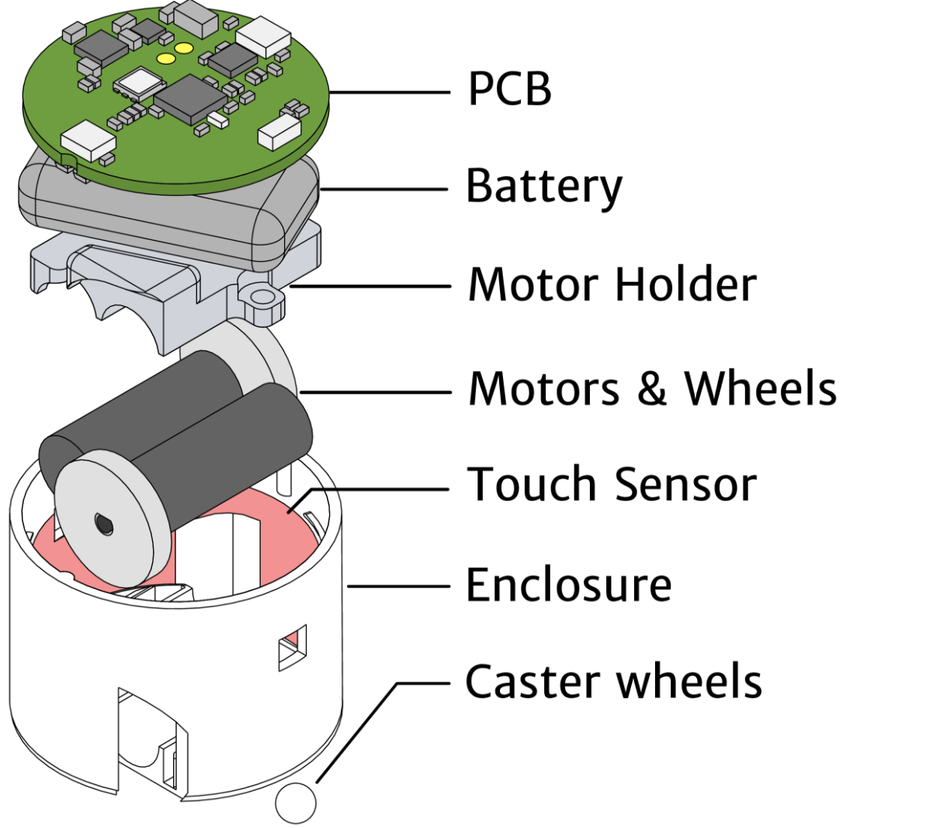
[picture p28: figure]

Overall Wire Connection:

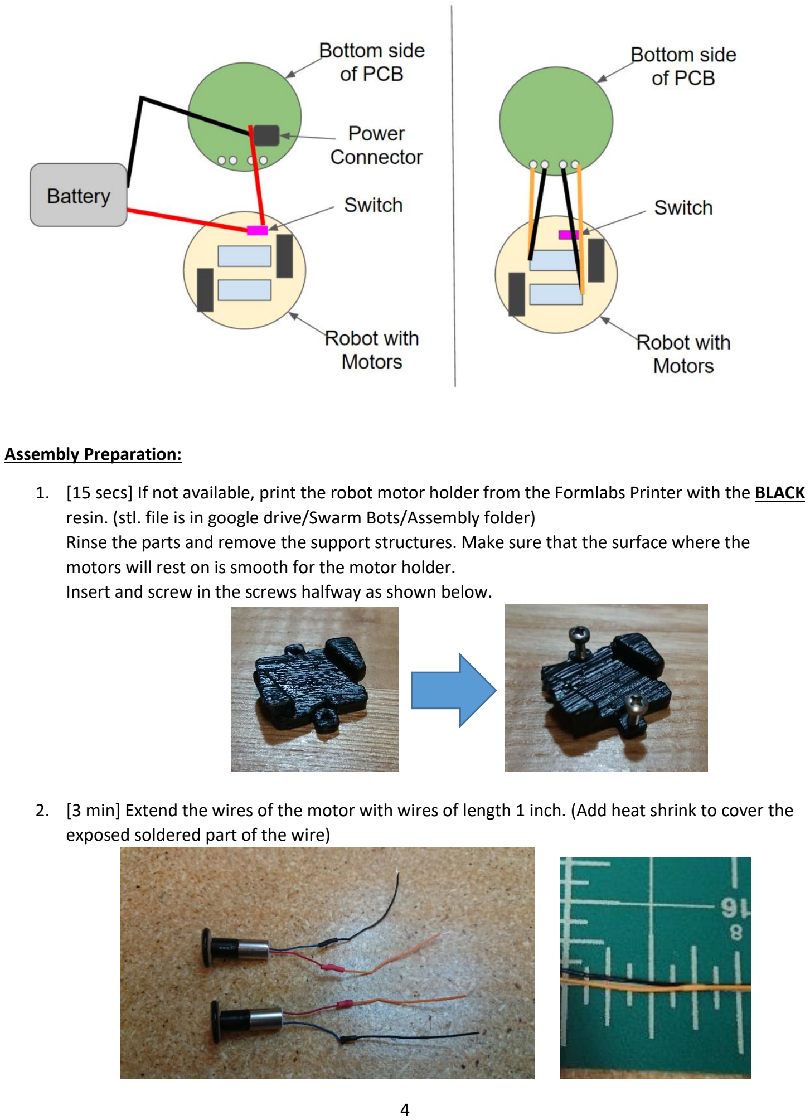
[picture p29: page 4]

Assembly Preparation:

1. [15 secs] If not available, print the robot motor holder from the Formlabs Printer with the BLACK resin. (stl. file is in google drive/Swarm Bots/Assembly folder)
Rinse the parts and remove the support structures. Make sure that the surface where the motors will rest on is smooth for the motor holder.
Insert and screw in the screws halfway as shown below.
2. [3 min] Extend the wires of the motor with wires of length 1 inch. (Add heat shrink to cover the exposed soldered part of the wire)

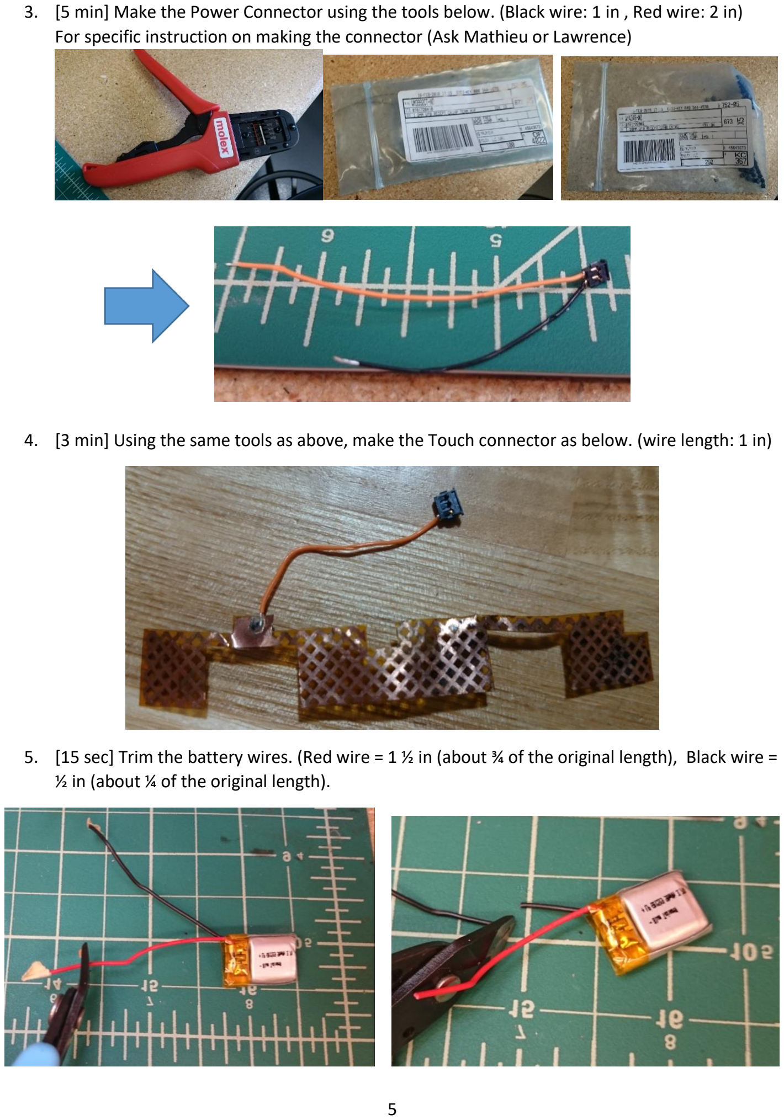
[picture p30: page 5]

3. [5 min] Make the Power Connector using the tools below. (Black wire: 1 in , Red wire: 2 in) For specific instruction on making the connector (Ask Mathieu or Lawrence)
4. [3 min] Using the same tools as above, make the Touch connector as below. (wire length: 1 in)
5. [15 sec] Trim the battery wires. (Red wire = 1 ½ in (about ¾ of the original length), Black wire = ½ in (about ¼ of the original length).

6. [3 min] Solder the red wire of the battery and red wire from the power connector onto the switch as shown. And solder the two black wires to each other. (*Before soldering, add in the heat shrink).

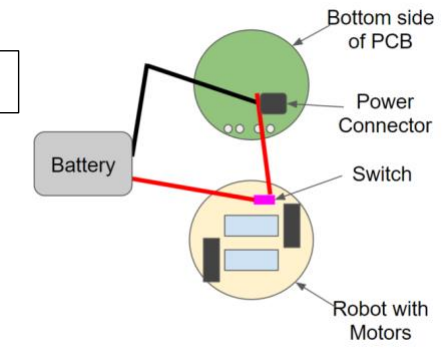
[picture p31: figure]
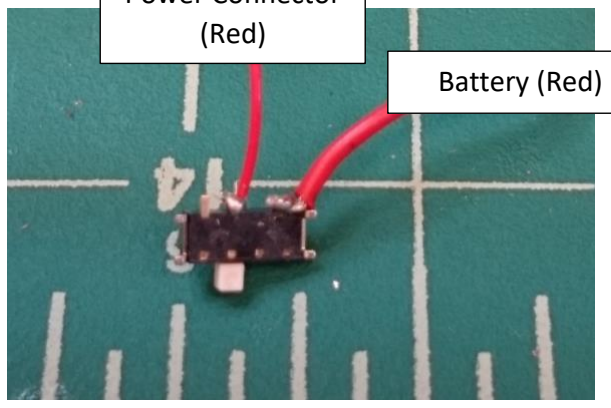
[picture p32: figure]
(Red); Battery (Red)

7. [15 sec] Add the wheels (O-ring + 3d printed part) to the motors. If the fit is not very tight, superglue the wheels to the motor.

Assembly Steps:

1. [10 secs] Insert two metal balls in the slots on the bottom of the 3D printed robot base as shown below on the left.

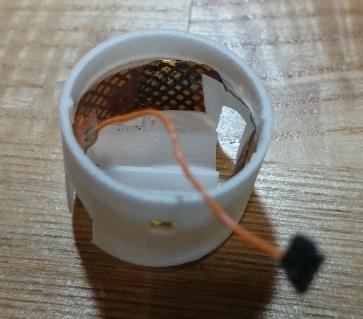
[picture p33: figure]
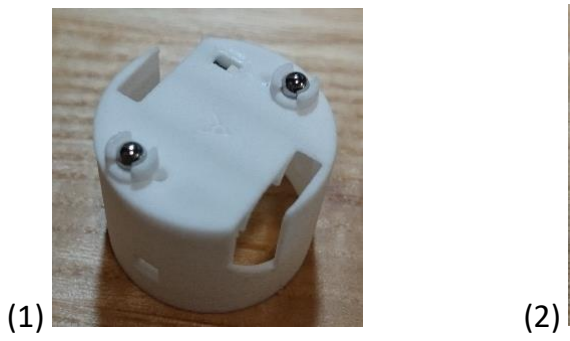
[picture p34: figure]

2. [1 min] Insert the touch circuit in the robot base as shown above on the right. Make sure the copper side faces outward and that the circuit is not interfering with the wheel hole, and is below the chamfer.
3. [15 sec] Wind the motor wires as below to prevent it from interfering with the other motor. Position the motor so the wires align vertically.

Power Connector

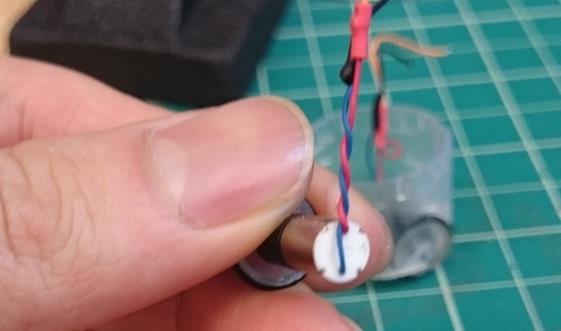
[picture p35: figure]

4. [1 min] Place the motors on the slots of the base and insert the switch into the robot base as shown. (Make sure the switch is in the right orientation, the metal side should be closer to the motors)

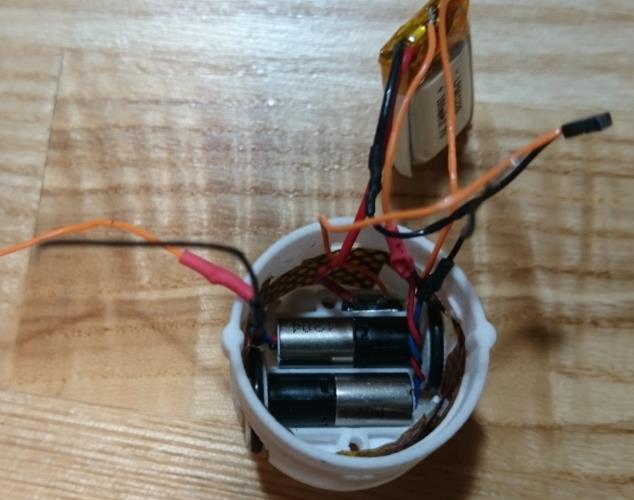
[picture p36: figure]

5. [1 min] Place the 3D printed motor holder + M2 screws on top of the motor and screw onto the robot base. (Make sure it is tight enough such that motors don’t spin around when you spin the wheels but don’t over-tighten as it may ruin the threads)
Make sure the motor holder is in the right orientation. On the side where the switch is, there should be a slight edge to hold the switch in place.

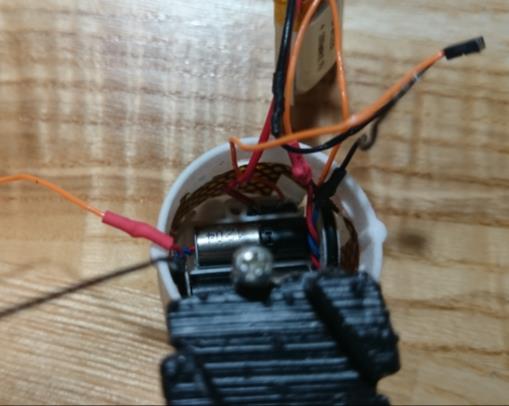
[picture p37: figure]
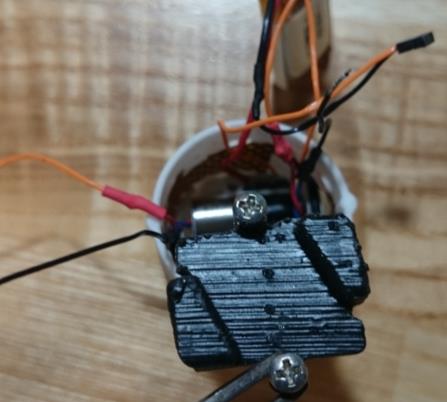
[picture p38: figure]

6. [15 sec] Double check that the robot is primary resting on the wheels rather than the castor wheels (metal balls).
7. [2 min] Solder the motor wires onto the PCB board as shown

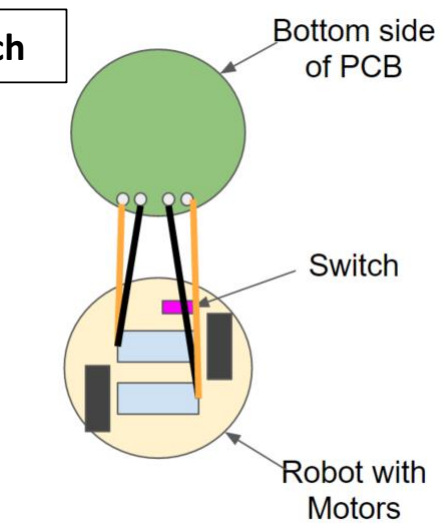
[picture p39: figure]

8. [30 sec] Place the battery on top of the motor holder. Connect the Power connector (2 sockets) to the PCB board. Connect the touch connector (3 sockets) to the PCB board.

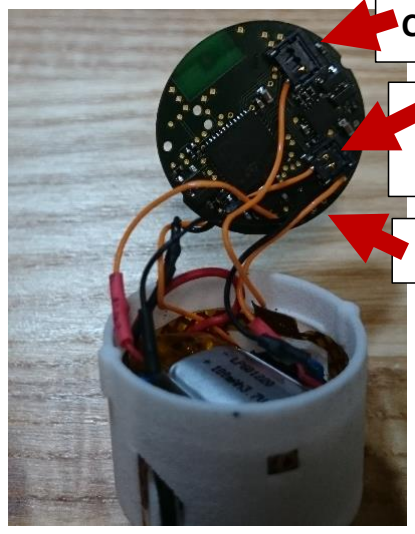
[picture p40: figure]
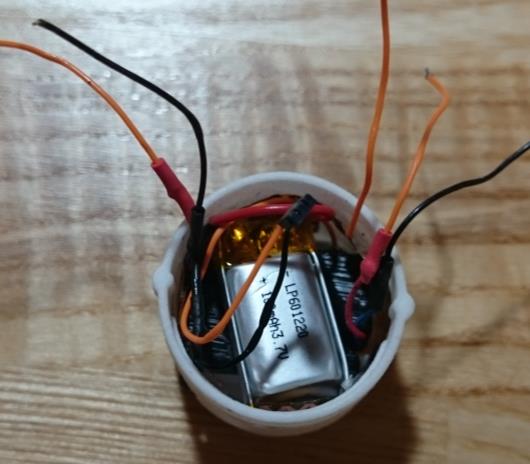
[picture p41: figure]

9. Evenly distribute the wires inside such that they are below the PCB chamfer and place the PCB board as shown below.

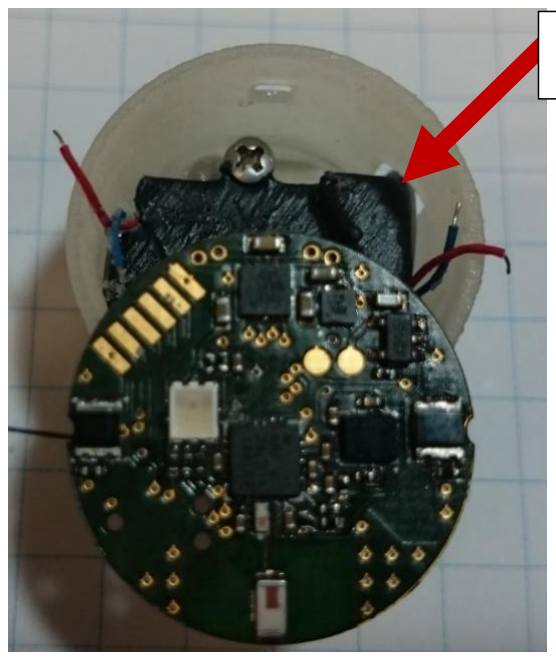
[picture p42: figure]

Switch

Switch

Touch
Connector

Power
Connector

Motors

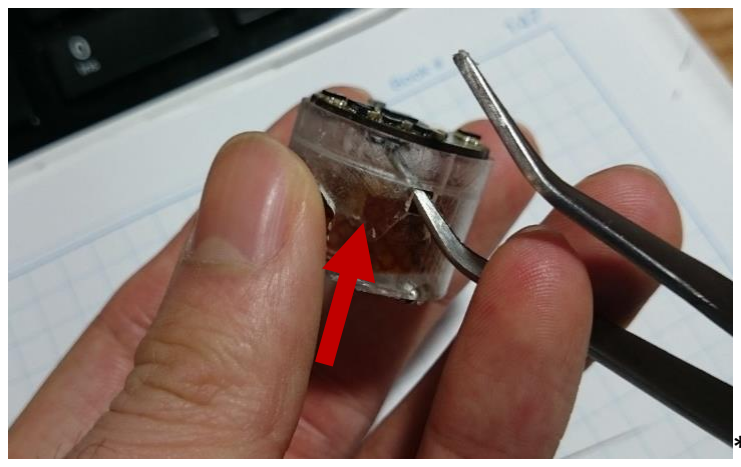
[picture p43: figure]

**

**To remove the PCB, use the thin long tool to push it up using the holes on the side.

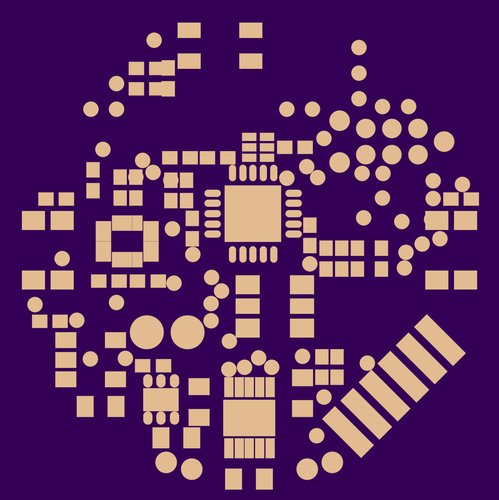
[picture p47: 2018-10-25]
Images/OG_boardTopSolderMask.png

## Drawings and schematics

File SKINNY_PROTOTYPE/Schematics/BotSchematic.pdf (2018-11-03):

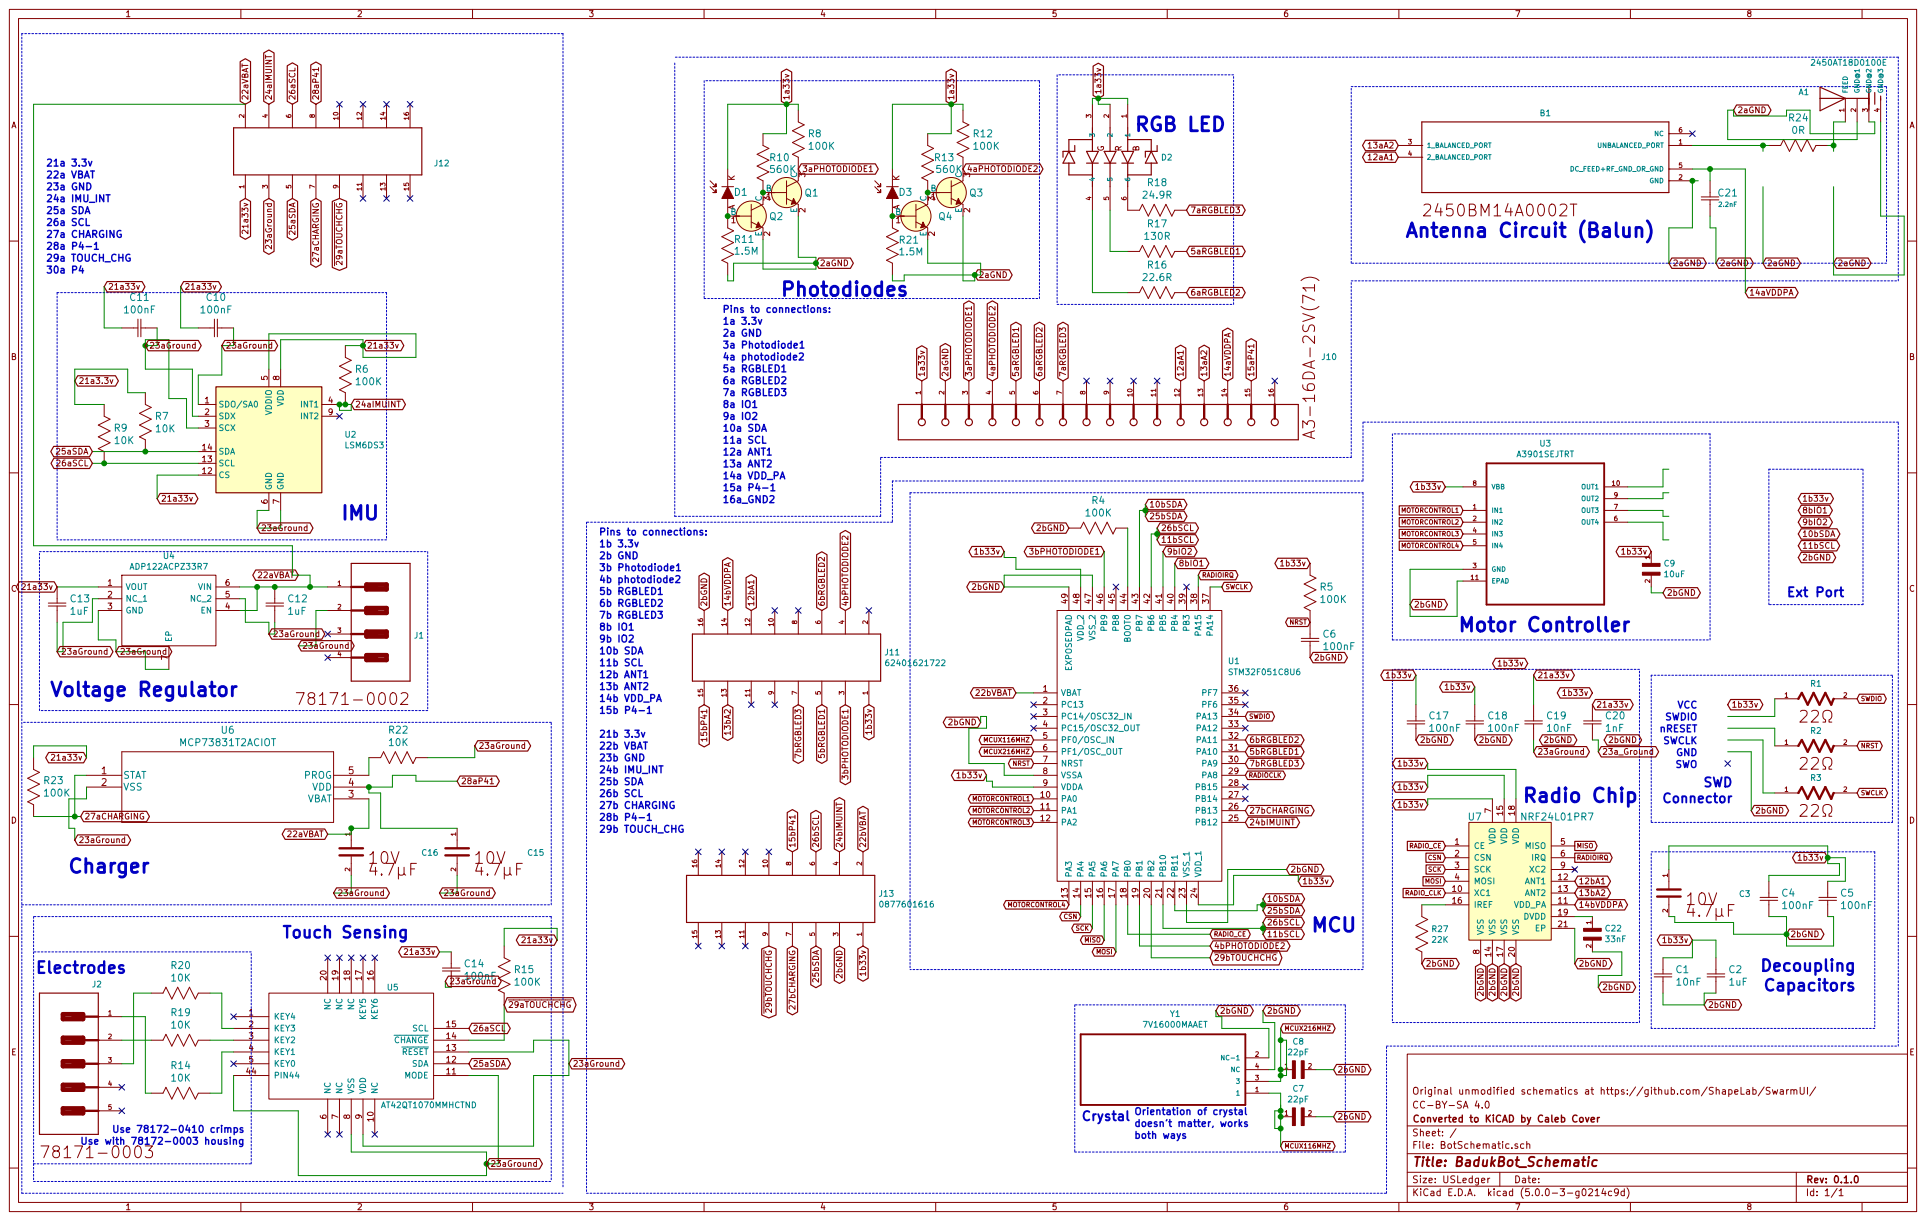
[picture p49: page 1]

22pF MCUX116MHZ MCUX216MHZ Crystal Orientation of crystal

File: BotSchematic.sch Sheet: / Converted to KiCAD by Caleb Cover CC-BY-SA 4.0 Original unmodified schematics at https://github.com/ShapeLab/SwarmUI/

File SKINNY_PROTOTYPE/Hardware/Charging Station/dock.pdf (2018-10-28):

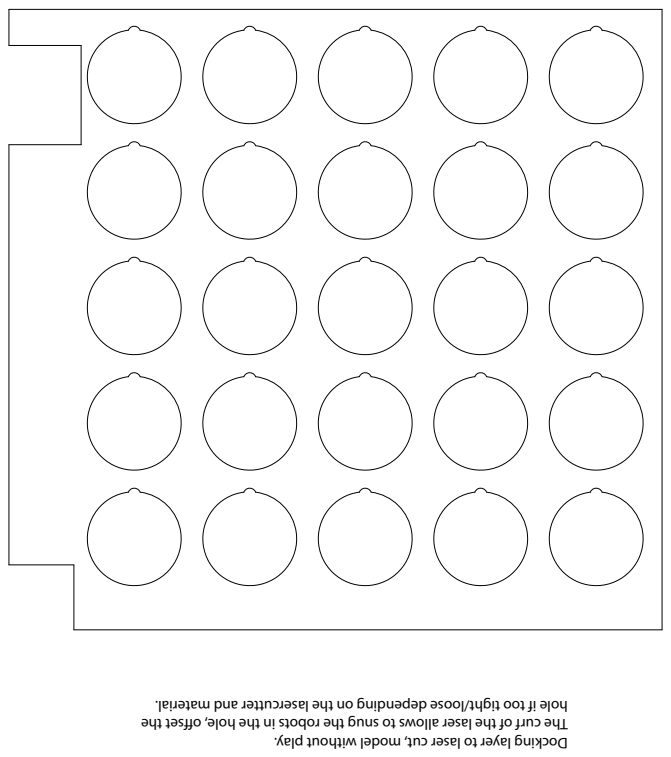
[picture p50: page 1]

hole if too tight/loose depending on the lasercutter and material.

set the ff The curf of the laser allows to snug the robots in the hole, o

Docking layer to laser cut, model without play.

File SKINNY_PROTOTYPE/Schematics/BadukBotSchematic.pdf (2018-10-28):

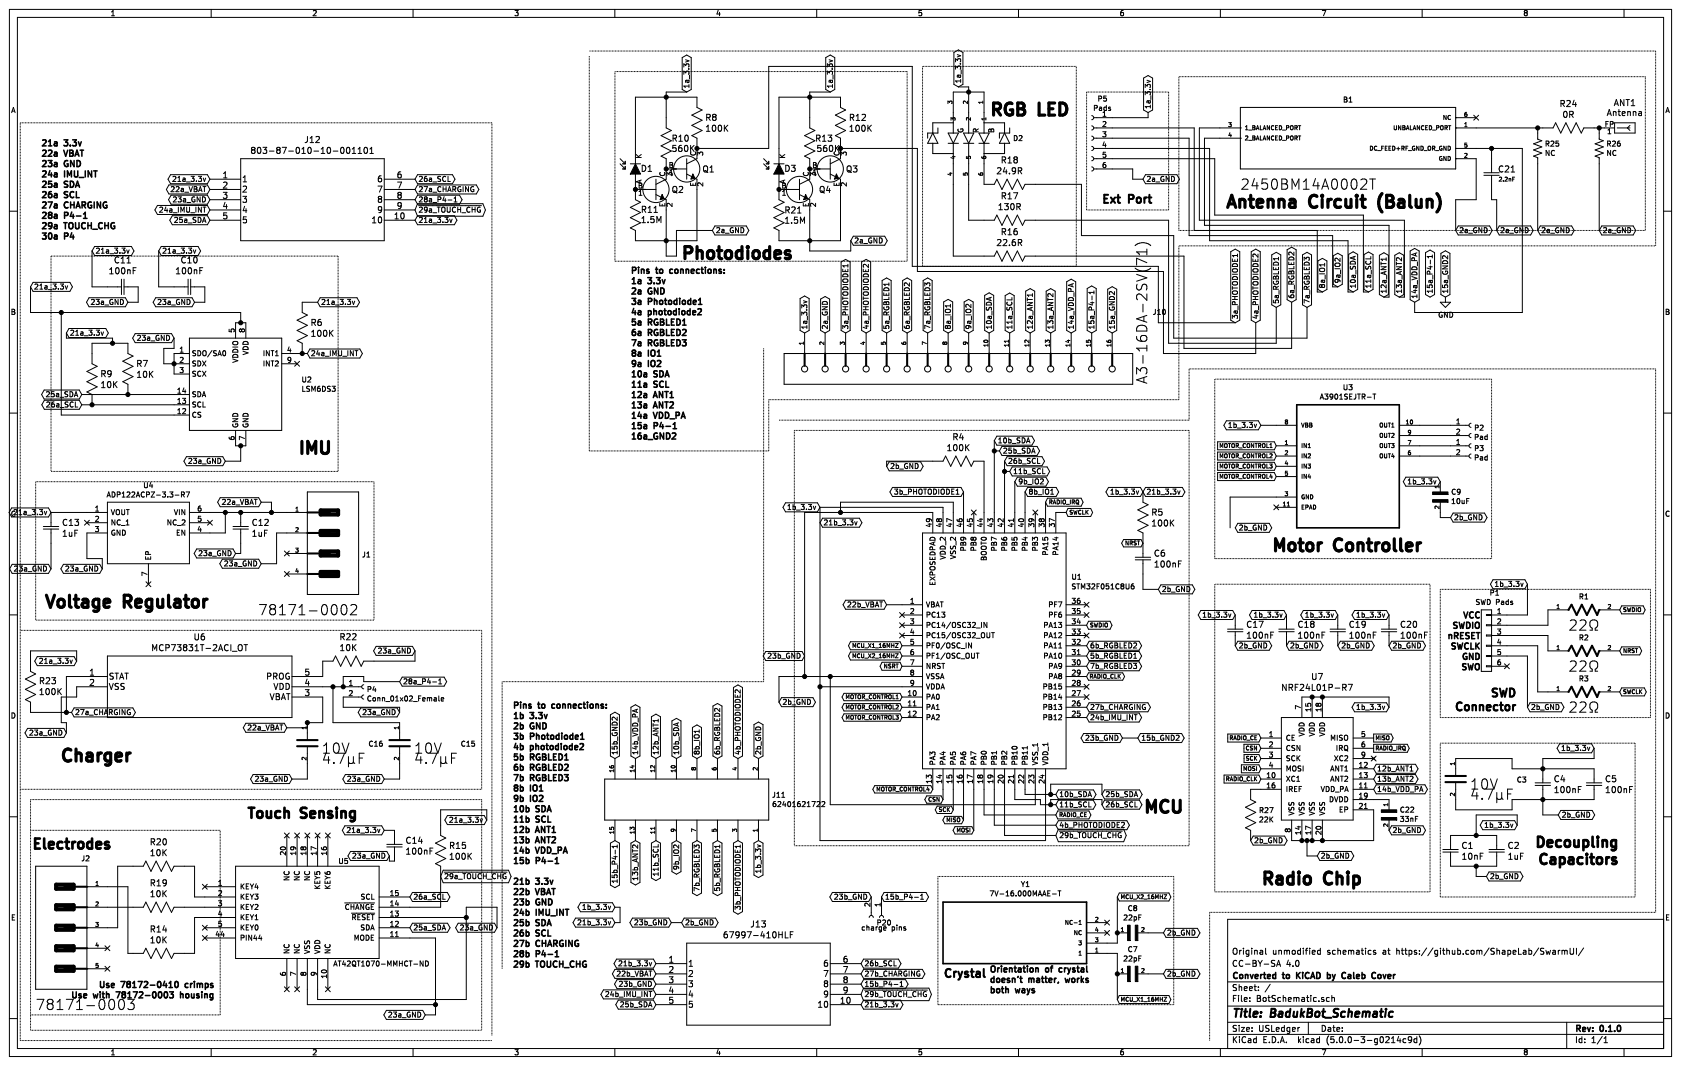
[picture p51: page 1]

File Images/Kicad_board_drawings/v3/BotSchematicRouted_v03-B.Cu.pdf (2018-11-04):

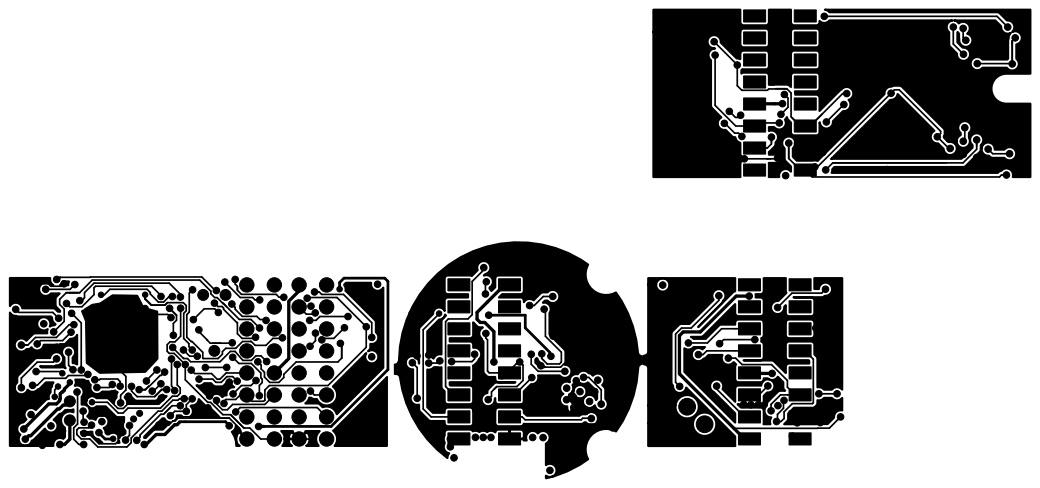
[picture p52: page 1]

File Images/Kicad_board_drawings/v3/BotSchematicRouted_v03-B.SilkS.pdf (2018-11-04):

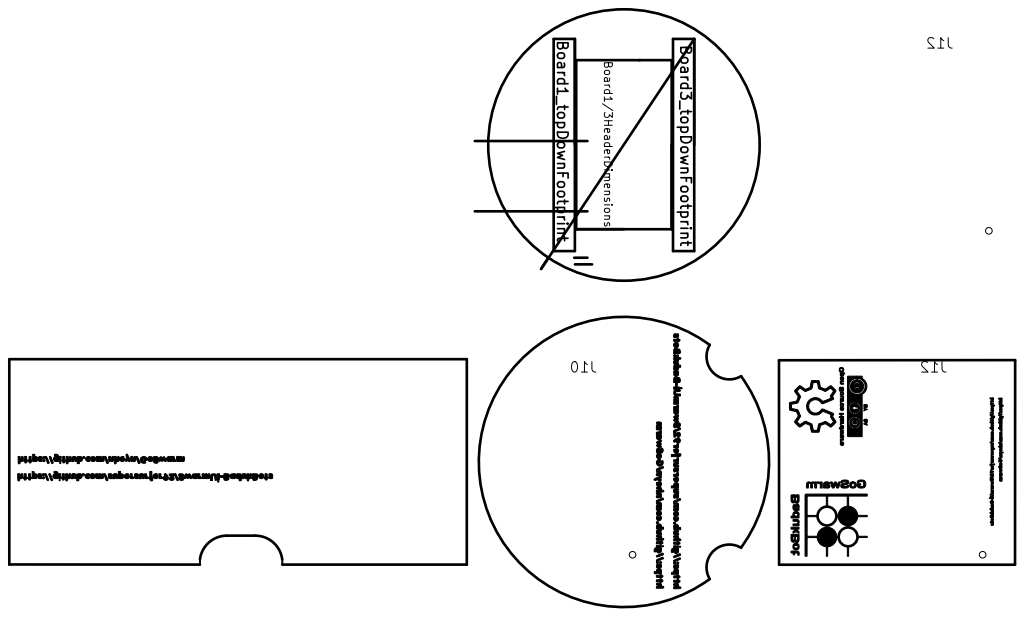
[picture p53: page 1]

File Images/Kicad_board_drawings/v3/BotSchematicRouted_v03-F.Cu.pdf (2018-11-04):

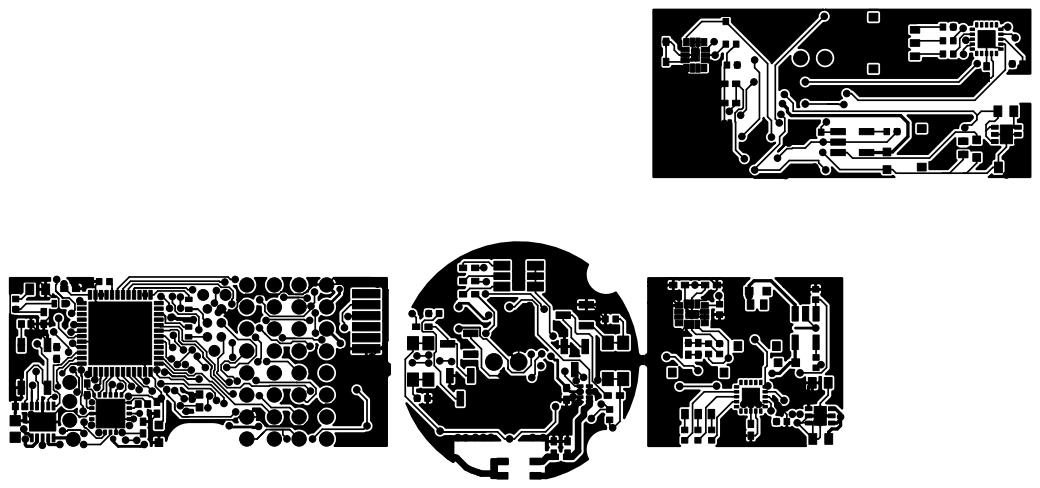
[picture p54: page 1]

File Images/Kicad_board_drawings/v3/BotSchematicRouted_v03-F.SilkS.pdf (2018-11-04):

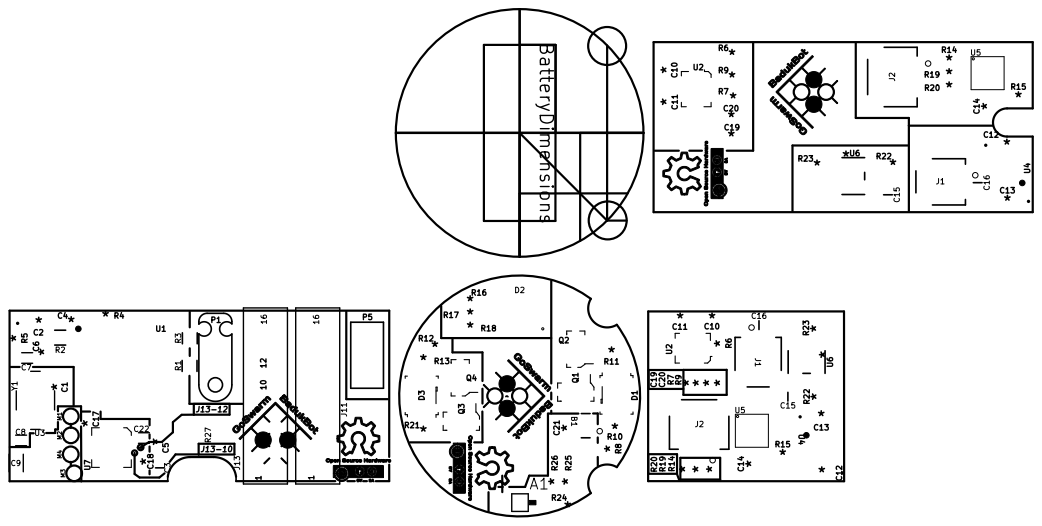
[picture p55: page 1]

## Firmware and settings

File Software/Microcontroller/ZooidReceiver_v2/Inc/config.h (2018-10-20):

/* Define to prevent recursive inclusion -------------------------------------*/
#ifndef __CONFIG_H
#define __CONFIG_H

#ifdef __cplusplus
 extern "C" {
#endif

/* Includes ------------------------------------------------------------------*/
#include "stm32f1xx.h"
#include "stm32f1xx_hal.h"
#include <__cross_studio_io.h>
#include <string.h>
#include "usbd_core.h"
#include "usbd_desc.h"
#include "usbd_cdc.h" 
#include "usbd_cdc_interface.h"

/*
  CONSTANTS DECLARATIONS
*/

#define USE_HSE

#define FALSE                                   0
#define TRUE                                    1
#define LOW                                     GPIO_PIN_RESET
#define HIGH                                    GPIO_PIN_SET

#define ON                                      TRUE
#define OFF                                     FALSE
#define false                                   FALSE
#define true                                    TRUE

///////////////////////////////////
//    COMMUNICATION CONSTANTS    //
///////////////////////////////////

#define RADIO_CHANNEL                           88  //channel at which you want to communicate through
#define PAYLOAD_MAX_SIZE                        32
#define ADDRESS_INCREMENT                       2
#define DEFAULT_ADDRESS                         0xF0F0F0F0D000
#define DEFAULT_ID                              0xFF
#define REFRESH_RATE                            60  //in Hz
#define REFRESH_PERIOD                          (uint32_t)(1000/REFRESH_RATE)
#define COMMUNICATION_TIMEOUT                   4000 //in ms
#define ANSWER_TIMEOUT                          2 // in ms
#define MAX_MESSAGES_LOST                       (uint32_t)(COMMUNICATION_TIMEOUT/REFRESH_RATE) //2000ms

#define NB_MAX_ROBOTS                           10
#define RECEIVER_ID                             250

///////// MESSAGE TYPES ///////////
//Operating messages
#define TYPE_UPDATE                             0x03
#define TYPE_STATUS                             0x04
#define TYPE_MOTORS_VELOCITY                    0x05
#define TYPE_ROBOT_POSITION                     0x06

//Configuration Messages
#define TYPE_NEW_ROBOT_REQUEST                  0xF0
#define TYPE_NEW_ROBOT_INFORMATION              0xF1

#define TYPE_REBOOT_ROBOT                       0xFF
  
/*
  DELAY TIMER DECLARATIONS
*/
#define MICRO_TIM                               TIM2
#define MICRO_FREQ                              100
#define MICRO_CLK                               1000000
#define MICRO_PERIOD                            (uint32_t)(MICRO_CLK/MICRO_FREQ)  /* Period Value  */
#define MICRO_TIM_CLK_ENABLE()                  __HAL_RCC_TIM2_CLK_ENABLE();
#define MICRO_IRQn                              TIM2_IRQn
#define MICRO_IRQHandler                        TIM2_IRQHandler
#define MICRO_IRQ_PRIORITY                      0 //3->0
/*
  LED DECLARATIONS
*/
#define LED_REDBLUE_GPIO_CLK_ENABLE()           __HAL_RCC_GPIOB_CLK_ENABLE()
#define LED_GREEN_GPIO_CLK_ENABLE()             __HAL_RCC_GPIOA_CLK_ENABLE()

#define RED_PIN					GPIO_PIN_1
#define RED_GPIO_PORT                           GPIOB
#define GREEN_PIN				GPIO_PIN_7
#define GREEN_GPIO_PORT                         GPIOA
#define BLUE_PIN				GPIO_PIN_0
#define BLUE_GPIO_PORT                          GPIOB

#define STATUS_PIN                              GPIO_PIN_6
#define STATUS_GPIO_PORT                        GPIOA

#define RGB_TIM					TIM3
#define RGB_FREQ				10000
#define RGB_CLK					1000000
#define RGB_PERIOD				(uint32_t)(RGB_CLK/RGB_FREQ)  /* Period Value  */
#define BLINK_FREQUENCY                         10
#define BLINK_PERIOD                            (uint32_t)(500/BLINK_FREQUENCY)
#define GREEN_CHANNEL				TIM_CHANNEL_2
#define RED_CHANNEL				TIM_CHANNEL_4
#define BLUE_CHANNEL				TIM_CHANNEL_3
#define STATUS_CHANNEL				TIM_CHANNEL_1
#define RGB_CLK_ENABLE()                        __HAL_RCC_TIM3_CLK_ENABLE()

/*
  RADIO DECLARATIONS
*/
/* Definition for SPIx Pins */
#define SPIx_SCK_PIN                            GPIO_PIN_3
#define SPIx_SCK_GPIO_PORT                      GPIOB
#define SPIx_SCK_AF                             GPIO_AF0_SPI1
#define SPIx_SCK_GPIO_CLK_ENABLE()              __HAL_RCC_GPIOB_CLK_ENABLE()
  
#define SPIx_MISO_PIN                           GPIO_PIN_4
#define SPIx_MISO_GPIO_PORT                     GPIOB
#define SPIx_MISO_AF                            GPIO_AF0_SPI1
#define SPIx_MISO_GPIO_CLK_ENABLE()             __HAL_RCC_GPIOB_CLK_ENABLE()

#define SPIx_MOSI_PIN                           GPIO_PIN_5
#define SPIx_MOSI_GPIO_PORT                     GPIOB
#define SPIx_MOSI_AF                            GPIO_AF0_SPI1
#define SPIx_MOSI_GPIO_CLK_ENABLE()             __HAL_RCC_GPIOB_CLK_ENABLE()
    
#define SPIx_CSN_PIN                            GPIO_PIN_15
#define SPIx_CSN_GPIO_PORT                      GPIOA
#define SPIx_CSN_GPIO_CLK_ENABLE()              __HAL_RCC_GPIOA_CLK_ENABLE()

#define SPIx_CE_PIN                             GPIO_PIN_6
#define SPIx_CE_GPIO_PORT                       GPIOB
#define SPIx_CE_GPIO_CLK_ENABLE()               __HAL_RCC_GPIOB_CLK_ENABLE()

#define RADIO_IRQ_PIN                           GPIO_PIN_7
#define RADIO_IRQ_GPIO_PORT                     GPIOB
#define RADIO_IRQn                              EXTI1_IRQn
#define RADIO_IRQ_GPIO_CLK_ENABLE()             __HAL_RCC_GPIOB_CLK_ENABLE()
#define RADIO_IRQ_PRIORITY                      1 //3->0

#define SPIx                                    SPI1
#define SPIx_CLK_ENABLE()                       __HAL_RCC_SPI1_CLK_ENABLE()

/* Definition for SPIx's DMA */
#define SPIx_TX_DMA_STREAM                      DMA1_Channel3
#define SPIx_RX_DMA_STREAM                      DMA1_Channel2

/* Definition for SPIx's NVIC */  
#define SPIx_DMA_TX_IRQn                        DMA1_Channel3_IRQn
#define SPIx_DMA_RX_IRQn                        DMA1_Channel2_IRQn

#define SPIx_DMA_TX_IRQHandler                  DMA1_Channel3_IRQHandler
#define SPIx_DMA_RX_IRQHandler                  DMA1_Channel2_IRQHandler

#define DMAx_CLK_ENABLE()                       __HAL_RCC_DMA1_CLK_ENABLE()

#define SPIx_FORCE_RESET()                      __HAL_RCC_SPI1_FORCE_RESET()
#define SPIx_RELEASE_RESET()                    __HAL_RCC_SPI1_RELEASE_RESET()



/* Uncomment the line below to select your USB clock source */
//#define USE_USB_CLKSOURCE_CRSHSI48   1
#define USE_USB_CLKSOURCE_PLL                   1

#if !defined (USE_USB_CLKSOURCE_PLL) && !defined (USE_USB_CLKSOURCE_CRSHSI48)
 #error "Missing USB clock definition"
#endif



/* Exported macro ------------------------------------------------------------*/
#define COUNTOF(__BUFFER__)   (sizeof(__BUFFER__) / sizeof(*(__BUFFER__)))
#define DEBUG_ENABLED() ( DEBUG )

extern void Error_Handler(void);


/* Exported types ------------------------------------------------------------*/
typedef uint8_t MotorDirection;
typedef uint8_t bool;

typedef struct
{
  uint16_t x;
  uint16_t y;
} Position;

typedef struct
{
  uint8_t type;
  uint8_t id;
} Header;

typedef struct 
{
  Header header;
  uint8_t payload[PAYLOAD_MAX_SIZE-sizeof(Header)];
} Message;

typedef struct
{
    int16_t ax;
    int16_t ay;
    int16_t az;
    int16_t gx;
    int16_t gy;
    int16_t gz;
    int16_t T;
} ImuRawData;

typedef struct
{
    float ax;
    float ay;
    float az;
    float gx;
    float gy;
    float gz;
    float T;
} MotionData;

typedef struct
{
    int16_t ax;
    int16_t ay;
    int16_t az;
} AccelRawData;

typedef struct
{
    int16_t gx;
    int16_t gy;
    int16_t gz;
} GyroRawData;

typedef struct
{
    float w;
    float x;
    float y;
    float z;
} Quaternion;

typedef struct
{
    uint8_t id;
    uint64_t pipeAddress;
    uint8_t payloadSize;
    uint8_t messageType;
    uint8_t watchdogTimer;

    uint8_t dataBuffer[PAYLOAD_MAX_SIZE];
}Robot;


#ifdef __cplusplus
}
#endif

#endif /* __CONFIG_H */

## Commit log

2018-10-20 Add files via upload
    Master BOM files for Zooids, Receiver, and Charger including supplier links, prices, tools needed, PCB stencils, etc.
    Sheet is for making 81 and 361 Zooids
    [Zooid_masterBOM_ALL.ods, Zooid_masterBOM_ALL.xls]
2018-10-20 Charger PCB Gerbers .zip
    Zipped Charging pad gerbers file to make it easy to upload to OSH Park, PCB Way, Seeed, etc.
    Issue with file on OSH Park for drill holes. Not sure if other PCB providers get the same errors when being uploaded.
2018-10-20 Zooid and Receiver zipped Gerber files
    Zipped Zooid and Receiver gerber files to make it easy to upload to OSH Park, PCB Way, Seeed, etc.
    When using the Zooid files to generate stencils not sure if bottom stencil needs to be mirrored for use with OSH Stencils solder paste stencil. Same for receiver.
    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
2018-10-20 Drill gerber fixed, need to fix slot drill gerber
2018-10-20 Drill gerber fixed
2018-10-20 Deprecated, use xls file
    [Zooid_masterBOM_ALL.ods]
2018-10-20 Tools, charger, receiver, etc updated
    [Zooid_masterBOM_ALL.ods]
2018-10-20 Drill Gerber scale corrected
    [zooidpcb.drl]
2018-10-20 Drill gerber updated
    [zooidreceiver_roundholes.drl]
2018-10-20 Updates to parts, tools, quantities, sources
    [Zooid_masterBOM_ALL.xls]
2018-10-20 Charging pad gerbers
2018-10-20 Updated Folder structure, deleted unnecessary gerber/PCB files
    [0.dat.step, 1.dat.step, 2.dat.step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]
2018-10-21 File and BOM Updates
    Updated BOM to include printed parts, pcb etching, tools, projector(s), and touch sensor;
    Added KiCAD files for Touch Sensor
    [TouchSensor.kicad_pcb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]
2018-10-21 Minor bom update
    Added playing surface notes
    [Zooid_masterBOM_ALL.xls]
2018-10-21 Notes in BOM, removed doc that wasn't readable in brower on github
    [Zooid_masterBOM_ALL.xls]
2018-10-21 Creating semi-separate workspace to make a BadukBot with smaller footprint and larger battery capacity
    [0.dat.step, 1.dat.step, 2.dat.step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]
2018-10-21 Added prototype idea for smaller bot; Small run manufacturing resources
2018-10-21 Proto files added
    [BadukBot_KiCADschematic.sch]
2018-10-21 Added Reflow setup
    [v1_0_bom.csv]
2018-10-21 Working on making a smaller bot for better projection space management
    [BotSchematic.kicad_pcb, BotSchematic.sch, ZooidPeripherals-SchDoc-2018-10-21-02-32-06.sch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]
2018-10-22 Converting Altium Schematic pdf to KiCAD Schematic
    [BotSchematic.sch, _saved_BotSchematic.sch]
2018-10-22 Completed KiCAD Schematic
    [BotSchematic.sch]
2018-10-23 BOM updates; Converted Altium Schematics pdf to KiCAD; New PCB design; First pass at routing with FreeRouting
    [BotSchematic.dsn, BotSchematic.sch, _Zooid_PROTOBOM_ALL.xls]
2018-10-24 PCB adjustments
    [BotSchematic.dsn, BotSchematic.kicad_pcb, _saved_BotSchematic.sch]
2018-10-24 renamed proto folder to BadukBot
    [0.dat.step, 1.dat.step, 2.dat.step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]
2018-10-24 directory change/organization
    [0.dat.step, 1.dat.step, 2.dat.step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]
2018-10-24 revert directory change
    [0.dat.step, 1.dat.step, 2.dat.step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]
2018-10-24 schematic/pcb changes
    [BotSchematic.sch, _saved_BotSchematic.sch]
2018-10-25 More work on the PCB
    [BadukBot.dsn, BadukBotsep.dsn, BotSchematic.sch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]
2018-10-25 Original board layer images added; Experiments with trace routing using FreeRouting and component placement in KiCAD
    [_Zooid_PROTOBOM_ALL.xls, offset.dsn, offset.kicad_pcb]
2018-10-26 Board adjustments for main board and topboard connectors
2018-10-28 Images of original board's layers; images of current work setup; updated schematics and BOM to change connectors; major boards revisions
    [BadukBot.dsn, BadukBot.kicad_pcb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]
2018-10-30 Routed PCBs pending optimization
    [BadukBot.kicad_pcb, BotSchematic.sch, BotSchematicRouted_v02.dsn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]
2018-10-31 Updates to the BOM; PCB changes
    [BotSchematicRouted_v02.kicad_pcb, _Zooid_PROTOBOM_ALL.xls]
2018-11-02 Updated copper cores; changed schematic naming flags for 3rd party BOM generator; added renders of board; added some datasheets
    [BotSchematic.sch, BotSchematicRouted_v02.csv, BotSchematicRouted_v02.kicad_pcb]
2018-11-03 Added images of the board; minor changes to BOM; Attempts to use KiCost to automate component shopping; Minor changes to copper pours on board
    Working on getting KiCost to work with the xml generated by KiCAD to make shopping for parts easy at Octopart. Looks to be approx $20 per board
    [BotSchematic.sch, BotSchematicRouted_v02 copy.csv, BotSchematicRouted_v02 copy.xlsx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]
2018-11-03 Rearranging files
    [BadukBot_Receiver.kicad_pcb, BadukBot_Receiver.sch, BotSchematicRouted_v02.kicad_pcb]
2018-11-04 Changed PCB for more compact component placement, shortened board 3, added images for the new layout
    [BotSchematic.copy.xlsx, BotSchematicRouted_v02.kicad_pcb, BotSchematicRouted_v03.kicad_pcb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]
2018-11-04 Reduced board sizes, results in $6 saved per 3 boards at OSHPark
    [BotSchematicRouted_v02.kicad_pcb, BotSchematicRouted_v03.kicad_pcb]
2018-11-04 Added images of v3 of the board
2018-11-06 board pics
2018-11-09 PCB revisions
    [BotSchematicRouted_v03.kicad_pcb]
2018-12-02 Changes to the PCBs for manufacturing
    [V3_noSilk.kicad_pcb, v3_mainBoard.kicad_pcb, v3_sideBoard.kicad_pcb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]
2018-12-02 Added pic of first batch of prototype boards
